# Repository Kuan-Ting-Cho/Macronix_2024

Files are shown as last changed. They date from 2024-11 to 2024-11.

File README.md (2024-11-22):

# Macronix_2024
[Human-Robot Collaboration of Intelligent Bipedal Robots in MultiLevel Warehousing_report](https://github.com/Kuan-Ting-Cho/Macronix_2024/blob/main/Human-Robot%20Collaboration%20of%20Intelligent%20Bipedal%20Robots%20in%20MultiLevel%20Warehousing.pdf)
## 競賽影片
競賽影片 (https://www.youtube.com/watch?v=QOL8G59Ion0)
## 模擬影片
模擬影片 (https://www.youtube.com/watch?v=DtHmWgVyCPI)
## 優勝獎
[第二十四屆旺宏金矽獎 半導體設計與應用大賽 優勝獎_獎狀](https://github.com/user-attachments/assets/30253aed-6e60-4f00-baa1-990223924b51)
## International and System Science and Engineering 2024 (ICSSE 2024)
[ICSSE 2024 conference paper](https://github.com/Kuan-Ting-Cho/Macronix_2024/blob/main/Mechanism%20and%20System%20Design%20of%20Linkage%20Driven%20Humanoid%20Robot.pdf)\
[ICSSE 2024_獎狀](https://github.com/user-attachments/assets/f3b2eac2-80f3-41f5-9eda-311fcf2eda83)

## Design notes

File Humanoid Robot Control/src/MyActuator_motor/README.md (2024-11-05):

# MyActuator_motor
This is the basic control of MyActuator motor using CAN bus communiccation. 
Basic setup and tutorials are in HackMD (https://hackmd.io/TwwChWEaTb-me8Ldjc6JkA?view).

NOTE: If you want to use Waveshare USB-CAN-A, then you neet to modify the file "serial_can.py" in original CAN package.
This is because Waveshare USB-CAN-A has unique frame format that is not supported in original CAN package. The CAN package I used in 2023/12/22 is python_can 4.3.1, there are some differences between each version. Be careful to use. And... good luck!

The latest pre-release can be installed with:
 '''
 pip install --upgrade --pre python-can
 '''

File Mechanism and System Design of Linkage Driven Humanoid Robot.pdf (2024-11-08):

Abstract— In this study, we present the design and implementation of a new humanoid robot lower body hardware structure. A four-bar linkage mechanism is used for the transmission to mimic the human leg muscles. The foot sole is designed to mimic the human arch, so that the robot can walk similar to the human gait. In addition, a comprehensive system architecture is established to control the robot.

I. INTRODUCTION

The humanoid robot has achieved a new milestone with the launch of the Tesla Optimus Gen 2 prototype [1]. In this paper, a new humanoid robot is proposed to mimic the human leg structure and the arch of the foot through a four-bar linkage mechanism [2] and foot soles design [3]. On the basis of high extendibility and maintenance, deep learning and algorithms are implemented to optimize and improve the robot system, ensuring that the robot can perform a variety of human actions and solving the phenomenon of labor shortage in modern industries.

II. METHODS AND RESULTS

The goals of robot’s leg design are to achieve light-weighting and mimic the structure of human legs which allows the center of mass of the bipedal robot to move upward, thus decreasing rotational inertia. In Fig. 1, Four-bar linkage mechanism is used for driving robot’s legs. This mechanism mimics the muscles contraction of human legs. All of four-bar linkages are parallel equal crank linkages. Except for the robot's driving links, which are made of high stiffness metal, lightweight materials are used. Carbon fiber tubes are used to connect the joints in the legs.

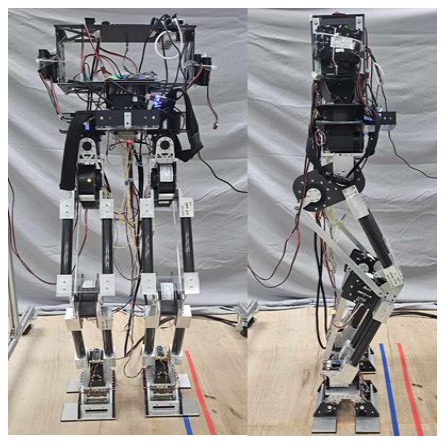
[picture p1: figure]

Figure. 1. The mechanism of the robot.

This work is supported by the National Science and Technology Council, Taiwan, R.O.C., under Grant NSTC 112-2221-E-006-155. The authors are with the aiRobots Laboratory, Department of Electrical Engineering, National Cheng Kung University, Tainan 70101, Taiwan ROC. (e-mail:
poetrydynasty@gmail.com, | j0988993487@gmail.com, | n26114201
@gs.ncku.edu.tw, n26114219@gs.ncku.edu.tw).
* Corresponding author: T.-H. S. Li (TEL: 06-2757575 ext.62363, E-mail: thsli@mail.ncku.edu.tw).

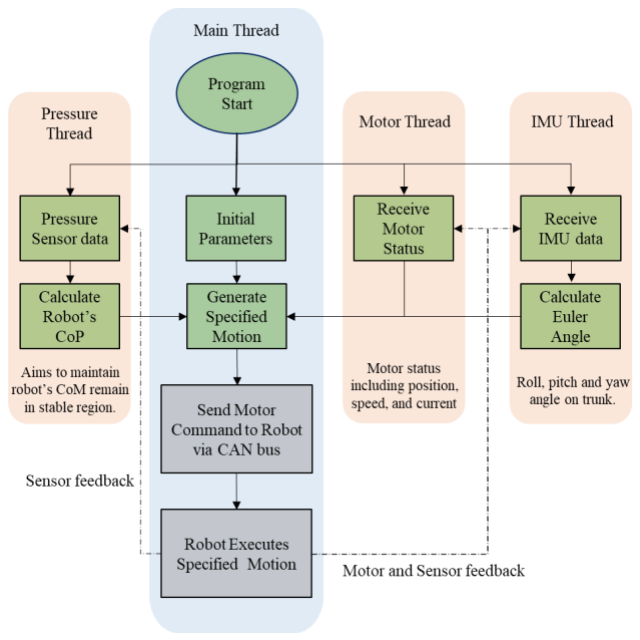
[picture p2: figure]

Figure. 2. The system architecture of the robot.
Regarding the design of foot soles, in order to reduce vibration during interaction with the environment, the mechanism mimics the arch of the human foot. Additionally, passive, rotatable joints are used at the front toe and rear heel sections as shown in Fig. 1.
The system architecture of this robot is shown in the Fig. 2. The control program consists of four threads, including the main thread and three others dedicated to receiving sensor data. The main thread is responsible for controlling the start and stop of each thread, receiving sensor data to generate appropriate motion commands, and transmitting them to the motors via the CAN bus. The other three threads are used to receive IMU data and compute Euler angles, receive motor angles and speeds, as well as receive pressure sensor data from the foot soles and calculate the robot’s center of pressure.

III. CONCLUSION
This paper presents an innovative design for a humanoid robot's lower body mechanism and system architecture, as well as the physical assembly and testing. In future work, we will finish the upper body of the robot and operate it to complete the walking and other dynamic testing so that it can be used in an actual-life situation.

REFERENCES

[1] “Optimus - Gen 2” https://www.youtube.com/watch?v=cpraXaw7dyc (accessed 2024/03/27.)
[2] Y. Zhang, L. Zhang, W. Wang, Y. Li and Q. Zhang, “Design and Implementation of a Two-Wheel and Hopping Robot With a Linkage Mechanism,” in IEEE Access, vol. 6, pp. 42422-42430, 2018.
[3] J. Sun, Z. Wang, M. Zhang, S. Zhang, Z. Qian, and J. Chu, “A Novel Metamorphic Foot Mechanism With Toe Joints Based on Spring-Loaded Linkages, ” in IEEE Robotics and Automation Letters, vol. 8, no. 1, pp. 97-104, Jan. 2023.

Kuan-Ting Cho, Chao-Chi Lee, Wei-Hsiang Huang, Yen-Ming Chen, and Tzuu-Hseng S. Li*

## Mechanism and System Design of Linkage Driven Humanoid Robot

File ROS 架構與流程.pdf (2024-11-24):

## ROS 架構與流程

節點與功能:

節點名稱 | 訂閱主 題 | 發布主題 | 功能描述
soldier | command | sensor | 接收馬達指令執行動作，計算感測器數 據，並發布感測器狀態
commander | sensor | command | 訂閱感測器數據，計算並生成執行動作與 平衡控制，並發布馬達指令

主題與數據:

主題名稱 | 資料來源 | 資料描述
sensor | soldier | 包含 IMU、壓力感測數據，以及馬達當前狀態
command | commander | 包含馬達目標位置、速度與控制模式指令

流程圖:

- [soldier 節點] →發布→ [sensor 主題] →訂閱→ [command 主題]
- [commander 節點] →發布→ [command 主題] →訂閱→ [sensor 主題]

節點詳細流程:

listener.py（接收指令並執行動作）

主要功能：

- 訂閱 “command” 主題，接收來自 “commander”的馬達指令。
- 根據收到的馬達目標指令與模式執行動作。
- 蒐集感測數據（IMU、壓力感測器），並發布到 “sensor” 主題。

核心流程：

- 初始化節點 “soldier”。
- 訂閱 “command”主題，更新當前馬達目標狀態。
- 執行動作（蒐集下一步的馬達狀態）。
- 周期性蒐集感測數據（IMU、壓力感測器）。
- 將馬達狀態與感測數據組合後發布到 “sensor” 主題。

talker.py（控制與指令發布）

主要功能：

- 訂閱 “sensor”主題，獲取感測器數據與馬達當前狀態。
- 執行動作控制，計算下一步馬達指令。
- 將計算結果發布到 “command”主題。

核心流程：

- 初始化節點 “commander”，建立訂閱與發布管道。

數據接收：

- 訂閱 “sensor” 主題，更新全域變數。
- imu_data：IMU 資料，用於平衡控制。
- l_fsr 和 r_fsr：左右腳壓力感測數據。
- pos：馬達當前角度。

動作生成與控制：

- 載入動作序列（CSV 文件中的馬達位置動作）。
- 插值生成平滑動作曲線，並根據感測數據控制目標馬達位置。
- 將馬達指令（目標角度、速度、模式等）發布到 “command” 主題。

“sensor” 主題（由 “soldier” 節點發布）

[[馬達 1 ID, 當前角度, 當前速度, 扭矩],

[馬達 13 ID, 當前角度, 當前速度, 扭矩],

[IMU_roll, IMU_pitch, IMU_yaw], [左壓力傳感數據 1, ..., 左壓力傳感數據 4], [右壓力傳感數據 1, ..., 右壓力傳感數據 4]]

“command”主題（由 “commander”節點發布）

[[馬達 1 ID, 控制模式, 目標角度, 目標速度, 扭矩, kp, kd],

[馬達 13 ID, 控制模式, 目標角度, 目標速度, 扭矩, kp, kd]]

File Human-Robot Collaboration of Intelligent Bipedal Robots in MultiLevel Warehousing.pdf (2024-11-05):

第二十四屆旺宏金矽獎

作品企劃書

# 智慧雙足機器人應用於多層 倉儲之人機協作

# Human-Robot Collaboration of Intelligent Bipedal Robots in Multi-Level Warehousing

## 參賽組別：應用組

## 參賽編號：A24-073

隊 | 長：卓冠廷
隊 | 員：李照棋、黃瑋翔、陳彥銘

摘要
本企劃設計及應用身長 126.4 公分之雙足機器人，著眼於下半身機構應用， 加入機構設計的巧思並開發系統架構，結合多種感測器資訊去對雙足機器人進行 控制。
在設計方面，團隊根據人體肌群，以四連桿傳動方式對機器人重心做調整， 不僅節省能源消耗，更是簡化機器人控制層面的難易度，同時也參考人體足弓， 設計了具緩震效果的腳掌，降低馬達與機構損耗，克服地形限制，更是讓雙足機 器人動作切合實體人類步態模式。
在應用方面，首先得建立雙足機器人步態數學模型，團隊成功將其運用於實 體機器人上，接著透過三種不同的場域測試進一步驗證，有負重走路、上下階梯 與不平坦地形的實驗，主打搬運機器人於多層倉儲會遇到的情境去研發，在基礎 的系統架構上加入不同演算法、強化學習等方式進行控制，最終成功將模擬的成 果於實體雙足機器人實踐。

一、前言
在現今社會中，高齡化對社會的影響越來越劇烈，缺工已成為產業難以解決 的問題之一，再加上 COVID-19 疫情的爆發，導致全世界的缺工問題更加嚴重。 在這樣的環境下，如果能將機器人應用於一些工作場域或是代替人類執行某些任 務，就能夠大大解決此問題。實際上目前許多工作場域都有慢慢引入機器人來替 代簡易的工作，但可以發現這些機器人的工作場域常常侷限於平面地面，無法跨 越樓層所帶來的限制，而雙足機器人則不受該種地形帶來的限制影響。 足型機器人在斜坡、階梯上往往較其它機器人有優勢。在空間沒有這麼寬廣 的超市倉儲內，雙足機器人因其下半身的獨特性，能更好地在該環境下移動。近 年來，越來越多公司投入雙足機器人的研發，如 Agility Robotic 的 Digit [1]、Boston Dynamics 的 Atlas [2]還有今年 Tesla 全新發表的 Optimus Gen 2 [3]，顯示出世界 知名公司也都致力於發展雙足機器人領域。然而，國內對於此方面的投入卻相對 十分稀少。最主要的原因在於此種機器人研究往往需要投入大量的資源才能夠實 現。因此，本計畫之一大目標便是利用這有限的資源，進行雙足機器人的開發和 研究，使其具備人機協作，甚至是不同機器人間的相互合作。

二、雙足機器人

1. 機構設計理念與目的
本團隊目前已開發雙足機器人的下半身機構如圖 1 與圖 2，同時也建立了 雙足運動數學模型。為了提高行走效率、儲存能量以及釋放動能，參考了人類腿 部結構與足弓進行設計。透過彈簧、馬達、連桿等各種元件的結合去建立了一個 強健的機構，同時具備緩衝功能，以極大程度地減少機體損傷的風險。此外，步 態模型的建立與感測器的回傳資訊實現了對機器人的精確掌控，使其能夠完成多 種預期中的行為和動作。
為了符合提出的應用場域，雙足機構的機構設計標準是輕量化以及減少能

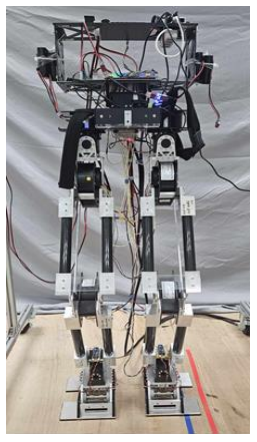
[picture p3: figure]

圖 1、機器人側視圖. | 圖 2、機器人正視圖. | 圖 3、機器人 CAD 圖.
量浪費，除此之外還需要有搬運重物的能力。透過模仿人類腿部的構造，讓雙足 機器人在運動過程中，可降低機器人與環境互動時所造成的振動，並運用連桿機 構傳動方式，使馬達能配置於臀部，提高雙足機器人腿部的重心位置，其目的是 增加腿部的靈活性，且由於執行需要抬腿的運動時，提高腿部重心能降低旋轉慣 性，同時也能降低馬達輸出時所消耗的能量，以增加馬達的壽命。 傳動方式上採用了四連桿機構如圖 3 反藍部分，透過連桿轉動使關節隨連 桿距離變化產生轉動，如同人類透過肌肉收縮使關節彎曲。使用四連桿的優點 有以下幾點，首先，可以將腿部的重心拉高，不需要將馬達配置在轉動關節位 置上，有效降低雙足的旋轉慣性，馬達也相對省力，再者使用四連桿可以限制 關節的轉動角度範圍，即使馬達突然失控也不會輕易造成機構受損，最後，雙 足機器人上的四連桿皆為平行四連桿，也就是說在關節限制範圍內，控制關節 的角度不需要考慮換算問題，馬達變動的角度即是關節屈伸的角度。 板材的部分主要以鋁件、POM、碳纖維板三者進行組裝，選材部分掌握一 些原則，如轉動摩擦的關節或需攻牙處需用鋁件，其餘則以碳纖維或 POM 材 質，連結關節轉動的部分使用光軸加上 C 型扣環，因其為受力點也是轉動點， 因此轉軸需要是金屬件降低摩擦並確保不容易形變，而 C 型扣環是防止關節之 間的相對滑動。板材雖然相對輕巧，但在強度上容易產生彎曲(bending)，由於 機器人總長 126.4 公分，腿長即佔 102.1 公分，若只用板材勢必要選剛度高的材 料，但這會相對增加機器人總重，因此採用管材並設計套筒去連接關節。為了 達到輕量化的目的，這裡選用了碳纖維管，碳纖維管不只具備了輕巧優勢，在 強度上也符合要求。
腳底板的設計如圖 4，為了降低與環境互動的震動和使雙足機器人行走能 夠更像人類的動作，外觀的設計上模仿了人類的足弓，並在前腳尖與後腳跟的 位置加上被動可旋轉的關節，原因是人在行走過程中前腳是腳跟先著地，而後 腳起步時腳尖是最後離地，透過這個被動旋轉的機構，使行走上能更貼近人類 步態。為達到被動旋轉的效果，採用了扭力彈簧如圖 5，扭力彈簧的彈力係數 不可以過小，否則容易造成機器人的不平衡，又因市面上扭力彈簧規格固定，

表 1、雙足機器人規格
高度(cm) | 126.4(腿長 102.1)
重量(kg) | 21.9
自由度 | 13
材質 | 碳纖維、鋁、POM

我們經過試驗方法去選擇合適的彈力係數，並在安裝時給彈簧一個預負載，使 其更有減振效果。旋轉軸的部分使用軸承加光軸的方式，並使用板件固定扭力 彈簧防止左右滑動如圖 5。

2. 系統架構:

A、硬體:
硬體除了設計理念中提到的部分，驅動主要由馬達來執行，馬達的部分採用 智能伺服馬達(圖 6)和盤式馬達(圖 7)作為驅動，前者具有高精度和高可靠性的特 性，同時支持多種通訊協定和控制模式，方便與其他元件協同工作，主要用於雙 足機器人的 Yaw、Roll 方向關節，即腰與臀部的關節，後者是一種無刷直流馬達， 具有高效率和低噪音的特性，並且內置了編碼器和驅動器，方便控制與調節，適 合用於雙足機器人的 Pitch 方向關節，即腿部的關節，帶動連桿進行傳動。 感測器的部分主要有慣性量測單元(Inertial Measurement Unit, IMU)(圖 8)以 及壓力感測器(圖 9)，前者用的是 Movella Xsens 開發的產品，其專精於慣性感測

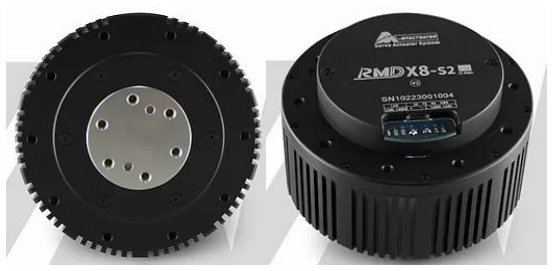
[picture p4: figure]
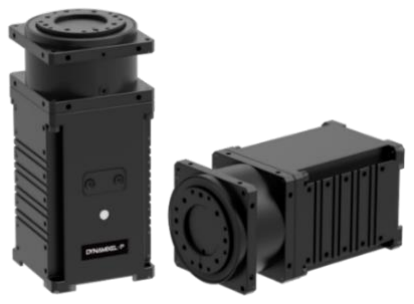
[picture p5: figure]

圖 6、智慧型伺服馬達. | 圖 7、盤式馬達.
圖 4、腳板側視圖. | 圖 5、扭力彈簧位置.

表 2、使用馬達規格表
| 智慧型伺服馬達 | 盤式馬達
重量(g) | 732 | 340 | 900
扭力(N.m) | 25.3 (at 24 V) | 5.1 (at 24 V) | 25 (at 48 V)
電壓(V) | 24 | 10.0~14.8 | 24、48
最大輸出 功率(W) | 132 | 20 | 110

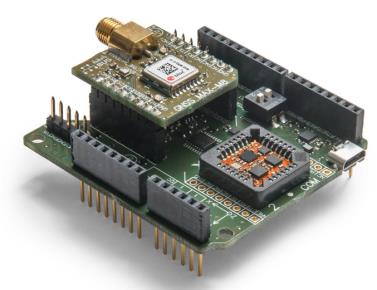
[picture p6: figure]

模組的設計生產與多傳感器融合演算法(Sensor Fusion)，我們將其配置於腰部， 蒐集機器人運動時的的尤拉角(Euler angle)、直線加速度與角加速度等資料，後者 選用薄膜壓力傳感器，置於腳底板四個角落，蒐集機器人運動時腳底受力狀況。

B、軟體:

系統的架構主要由四個線程(Thread)組成，分別有 Main Thread、Pressure Thread、Motor Thread、IMU Thread。主線程負責控制每個線程的啟動與停止， 接收感測器資料以產生運動命令，並透過 CAN bus 將其傳輸到馬達。另外三個 線程用於接收馬達角度、速度、IMU 與壓力感測器的資料。

(1)、感測器資料前處理與分析:

由於雙足機器人運用不同馬達進行運作，在接收馬達回傳值時，容易遇見回 傳時間不一的問題，因此在資料前處理上會適時的延遲，使馬達回傳時間盡量達 成一致，方便後續閉迴路控制做使用。IMU 的回傳資料則是經解碼後透過將四元 素轉換為尤拉角去使用，偵測機器人轉向之偏移幅度，作為步態修正之依據。壓 力感測器的量測需要根據機器人總重量去選擇合適的電阻值，資料前處理上會先

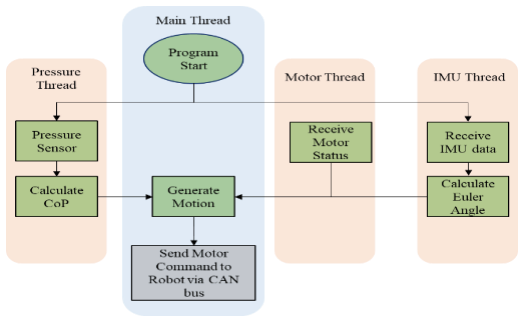
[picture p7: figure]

圖 10、雙足機器人之基礎系統架構

圖 8、Xsens MTI-7-DK IMU [4]. | 圖 9、薄膜壓力傳感器 [5].

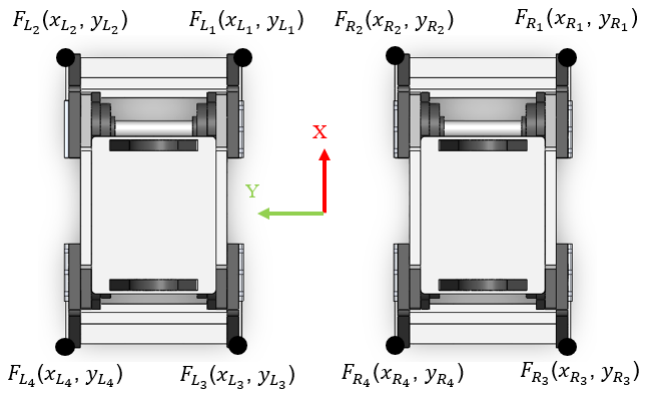
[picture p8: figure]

進行根據機器人實體情形進行雜訊濾波，防止因雜訊導致壓力中心位置的計算偏 差擴大，處理過後的資訊會用來分析機器人模型的 Center of Pressure(CoP)偏移。 壓力感測器裝置於機器人足部，左右腳的四個角落外圍各裝設一顆壓力感測器， 用夾層方式於腳底板與踏墊間加裝壓力感測器，如此一來，在機器人腳部未接觸 地面時，仍可繼續得到壓力偏移值，分別對雙腳各四個壓力感測器計算 CoP 之 x 與 y 位置，如(1)-(2)與圖 11 所示。

4 | 4
1 | 1
4 | 4
1 | 1
Ri | Ri | Li | Li
i | i
CoP
| Ri | Li
i | i
F x | F x
X
F | F
= | =
= | =
- | + | ·
=
| +
∑ | ∑
∑ | ∑
， | (1)
4 | 4
1 | 1
4 | 4
1 | 1
Ri | Ri | Li | Li
i | i
CoP
| Ri | Li
i | i
F y | F y
Y
F | F
= | =
= | =
- | + | ·
=
| +
∑ | ∑
∑ | ∑
。 | (2)

(2)、步態產生器數學模型:

為了讓雙足機器人能順利行走，一普遍且容易實現的步態模型為線性倒單擺 (Linear Inverted Pendulum Model, LIPM)，只需使用有限的物理結構資訊，即可生 成雙足機器人的步態。假設一個由點質量和無質量伸縮腿組成的倒單擺來模擬一 條腿支撐身體時狀況，其質心位置 x(t)以及質心速度ẋ(t)可以表示為:

x(t) = (x(0) − px) cosℎ cosℎ (
t
Tc

) + Tcẋ(0)sinℎ (
t
Tc

) + px，

(
3)

ẋ(t) =

(x(0)−px)
Tc

sinℎ sinℎ (
t
Tc

) + ẋ(0)cosℎ (
t
Tc

)。

(
4)
將此結論進一步推廣到三維的線性導單擺模型之中，分為 x-z 平面與 y-z 平 面進行推倒，得出 x 與 y 方向上的質心位置與速度，以實現的步行控制。之後將 LIPM 得出的結果透過特定的轉換即可套用於我們的機器人身上，生成出我們所 需要的動作。
為了能夠控制機器人的各關節，有必要進行一系列的數學推導來找出其中的 角度與位置關係。在機器人領域中，順向運動學（Forward Kinematics）是一個重

圖 11、壓力感測器安裝位置.

圖 12、機器人正視圖. 圖 13、機器人 45°視圖. 圖 14、機器人側視圖. 要的概念。它用來描述機械系統中各個部分相對於參考點或參考座標系的位置和 方向，透過順向運動學，可從給定的機械系統關節角度中，計算末端點的位置和 方向。為了建立出順向運動學，必須先定義出雙足機器人的 Denavit-Hartenberg （DH）表，DH 表的每一行需從機器人的前後關節找出資訊，其中包含四個參數：
1. θi： 繞著前一個 z 軸的角度，從舊的 x 軸到新的 x 軸。
2. di： 沿著前一個 z 軸到共同法線的偏移量。
3. ai： 共同法線的長度
4. αi： 繞著共同法線的角度，從舊的 z 軸到新的 z 軸。
透過 DH 表，我們可以在機器人的雙足上建立坐標系(圖 12-圖 14)。在設計 的機器人身上，每隻腳各有 6 個自由度，分別是髖關節上的 Yaw(R1, L1 )、 Roll(R2, L2 )與 Pitch 軸(R3, L3 )、膝蓋的彎曲 Pitch 方向(R4, L4 )以及腳踝的 Pitch(R5, L5)跟 Roll 方向(R6, L6)，其中 Z 軸為馬達旋轉方向，其中原點的部分設 置在髖關節中 Yaw 方向(R1, L1)旋轉的馬達中心，表 3 呈現雙足機器人的 DH 參 數。
表 3、雙足機器人的 DH 表.
i | θi | ai | αi | i d
1 | | | | d1

2

3 | 90° 0 | L2 L1 | −° 90 90° −° 90 90° L6 0 | 2 d L3 L4 L5 d3
4 | 2.74° | | 0 | 0
5 | -2.74° | | | 0
6 | 0 | | 0 | 0

1

cos | cos | sin | sin | sin | cos
sin | cos | cos | sin | cos | sin
0 | sin | cos
0 | 0 | 0 | 1
i | i | i | i | i | i | i
i | i | i | i | i | i | i | i
i
i | i | i

a
a
H
d
θ | α | θ | α | θ | θ
θ | α | θ | α | θ | θ
| α | | α

−

é | ù −
ê | | ú
−
= ê | | ú
ê | | ú
ê | ú ë | û
， | (5)

6
E

0 0 -1 0
0 1 0 0
1 0 0 0
0 0 0 1

H

é | | ù
ê | | ú
= ê | | ú
ê | | ú
ê | ú ë | û
， | (6)

式(5)顯示的是轉換矩陣，其包含了每個關節的位置與方向資訊，透過將 DH 表中的參數帶入，可以得出機器人每個關節的轉換矩陣。式(6)表示踝關節 Roll 方向的馬達座標到腳底板座標的轉換矩陣，式(7)表示了原點的坐標轉換到 末端點坐標:

| | | | | | | | | 11 | 12 | 13 | 0 ,
0 | 0 | 1 | 2 | 3 | 4 | 5 | 6 | 0 | 21 | 22 | 23 | 0 ,
E | 1 | 2 | 3 | 4 | 5 | 6 | E | E
| | | | | | | | | 31 | 32 | 33 | 0 ,

= P =

0 | 0 | 0 | 1 Ex
| | | Ey
| | | Ez
r | r | r | P
r | r | r | P
H | H H H H H H H
r | r | r | P
é | ù
ê | ú
= | ê | ú
ê | ú
ê | ú ë | û
。 | (7)

然而，在實際情況中，更多的時候我們已知機器人到達的目標位置，因此需 要反過來求得關節角度，這時就需要運用到逆向運動學(Inverse Kinematics)，而 每個關節角度可以透過式(7)左右等式相等來計算出，將線性導單擺模型規劃的 步態軌跡反推回每個馬達所需執行的角度命令，實現各式各樣的動作。

三、不同任務之實現

1. 負重靜態與動態平衡即時控制
A. 簡介
本章節會介紹雙足機器人在運送貨品時所需的靜態與動態平衡技術。由於本 團隊雙足機器人的行走步態是使用線性倒立擺模型控制機器人的行走軌跡，其為 開迴路的控制方法，若直接將貨品放到雙足機器人上行走，機器人會因重心不穩 而摔倒。因此本章節將針對此問題提出負重演算法以及平衡控制器，使雙足機器 人再負重時得以穩定行走，使其順利完成運送貨品任務。
B. 控制系統架構
圖 15 為本章節的控制系統架構圖，首先雙足機器人是由姿態控制器來做出 動態或是靜態的姿態，這裡所指的動態為 LIPM 產生的步態，靜態則是雙足機器 人的初始穩定姿態。根據姿態控制器的輸出，平衡控制器會決定要採用單腳或者 是雙腳的補償平衡，補償的多寡會由馬達當前狀態、慣性測量單元(IMU)和機器 人腳底板裝設的壓力感測器來決定。若是在靜態的情形下，雙足機器人會根據壓

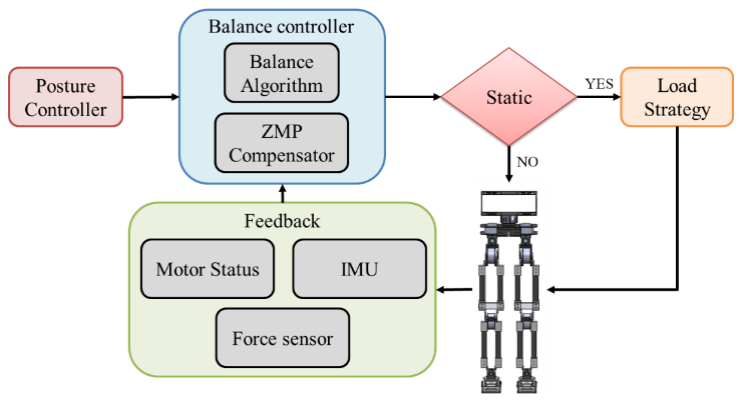
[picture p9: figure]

力感測器來判斷雙足機器人是否被裝載貨品，根據情況啟用負載緩衝策略，使機 器人不會因為裝載重物而失去平衡摔倒。最後總和所有控制器的輸出至雙足機器 人每顆馬達做出理想的平衡姿態。

C. 平衡控制器
無論雙足機器人的狀態為動態或靜態，所有良好的動作都是基於雙足機器人 在保持平衡的狀態下產生，因此保持平衡是不可或缺的要素。尤其對大型機器來 說，因為重心較高，在動作的控制上也會變得更加困難，因此為了使雙足機器人 有更好的表現，平衡控制器的存在成為關鍵。此章節所提出的平衡控制器分為兩 個部分，第一部分為平衡演算法，第二部分為零力矩點(ZMP)補償器，而兩部分 輸出的總和為平衡控制器的輸出。平衡演算法流程圖如圖 16，並分成靜態以及 動態。
首先雙足機器人在靜態時通常保持著雙腳對齊貼平地面，且質心投影位置在 雙腳中心的位置，以利接下來運動，然而外在環境的變化如地板傾斜或外力干擾， 會使質心偏離雙腳中心不利於下一個動作，甚至最嚴重導致摔倒，為了解決這個 問題，此演算法提供了適應環境變化的能力。根據兩隻腳的馬達角度回授，透過 順向運動學求得兩隻腳的末端執行器(End effector)位置以及旋轉矩陣，在前述所 提的靜止狀態下，左右腳的旋轉矩陣必定相同，由此可以得知雙腳末端執行器座 標相對質心座標的旋轉情況，而 IMU 回授可得知質心座標傾斜多寡，為了使質 心座標保持在平衡位置，此演算法將質心座標的傾斜角度乘上權重值後加入旋轉 矩陣，末端執行器位置也會隨著傾斜而調整，再透過逆向運動學映射回各個馬達 做即時補償，達到質心座標平衡的目標。
在動態的部分，步態週期分為單腳支撐和雙腳支撐兩種階段，支撐腳是行走 保持平衡的關鍵，此演算法主要是補償單腳支撐階段，因為雙足機器人在行走時 雙腳支撐是為了將重心轉移至另一支撐腳，其時間遠小於單腳支撐階段，因此演 算法將轉移重心前半段的支撐腳視為後腳，而後半段的支撐腳視為前腳。由於 LIPM 產生的步態質心座標並不會轉動，因此可以根據 IMU 回授做補償。動態補 償方式與靜態有兩點不同，第一是權重值較小，因為在行走情形下做較大幅度的

圖 15、負重平衡控制系統架構

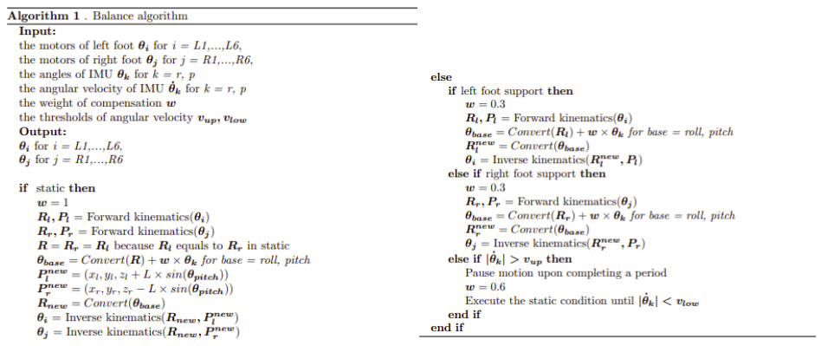
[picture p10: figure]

圖 16、平衡演算法
補償會導致質心速度方向改變太大，導致機器人摔倒，因此找到適合的權重值更 有助於行走時的穩定性，根據實驗結果在行走時權重值為 0.3 最穩定。然而在一 連串的動作下，雙足機器人可能會因外力導致質心速度改變偏離理想運動軌跡， 因此若發生質心速度高於平常穩定行走的閥值時，演算法會在完成當前行走週期 後將動作暫停，並進入暫時的靜態平衡直到質心穩定，此時的權重值不可與完全 靜態時相同，因為此時的質心較不穩定，若權重值太大會導致過度補償，根據實 驗結果權重值為 0.6 時可最快穩住質心。
在執行平衡演算法時，必須確保腳底板是貼平地面，因此提出零力矩點補償 器來解決此問題。根據腳底板的壓力感測器所回授的類比訊號，可以通過(8)至 (11)式獲得兩隻腳的零力矩點位置：

Zv =

(F1 + F4

)
(F2+F3+ε)
， | (8)

Zx =

Lx × Zv
(1 + Zv

)

−

Lx
2
， | (9)

Zℎ =

(F1 + F2

)
(F3+F4+ε)
， | (10)

Zy =

Ly × Zℎ
(1 + Zℎ

)

−

Ly
2
， | (11)

其中Zx、Zy為零力矩點座標，Lx、Ly為腳板的長與寬，ε為極小數值，其目的 是為了防止(8)、(10)式的分母為零，因為將座標零點設定在腳板中心如圖 17， 因此需要減去一半的腳板長寬。零力矩點補償器透過調整腳踝的 Roll 和 Pitch

圖 17、零力矩點座標參數示意圖

方向的馬達來達成目標，控制方式是採用 PD 控制器如下(12)、(13)式：

θi = Ki(Zi,y − Zi,y

d

) + Di(Ż

i,y − Ż
i,y

d
)， | (12)

θj = Kj(Zi,x − Zi,x

d

) + Dj(Ż

i,x − Ż
i,x

d
)， | (13)
其中i = R6, L6、j = R5, L5表式左右腳，因此補償器總共會有 4 組 PD 參數， 針對腳踝四顆馬達進行角度調節。然而要同時找到 4 組最佳的參數並不容易， 為了解決此最佳化問題，此章節使用元啟發式演算法根據設定好的訓練環境計 算適性函數(Fitness function)找尋最佳解，而訓練環境和適性函數的設計將影響 是否能找到最佳解的關鍵。
為了有效尋找，訓練環境由多階段的任務組成，其中包含地面旋轉、外力 干擾以及負重行走，任務總長為 2500 個時間步長(Time step)，每個時間步長為 0.02 秒，三個任務長度分別 1000、500、1000 時間步長，為了縮短總訓練時 間，當質心高度小於設定閥值時則判定雙足機器人摔倒提早結束訓練。在地面 轉動的任務會分為三個階段，其分別為對 Roll 方向旋轉、對 Pitch 方向旋轉、 對 Roll 和 Pitch 方向同時旋轉，旋轉方式如(14)式：

θ(t)ground =

π

18 × sin (
t × 2π
Tg
)， | (14)

其中Tg為地面轉動週期，長度為 250 個時間步長，在這時段內地面會依據設定 方向旋轉正負 10 度。在外力干擾的任務中，設定在指定時間點對機器人施予 195 N 的外力，其方向分為 x 和 y 方向。負重行走任務是在指定時間點會負載 重物，平衡後行走至時間結束，負載重量為 2 kg。
在適性函數的設計上，去計算左右腳每個時間步長在 x 與 y 的零力矩點座 標位置與速度與理想狀態差的絕對值，最後將所有值總和作為其訓練適性值 (Fitness value)，然而因為有提早結束訓練的機制存在，在被判定提早結束時， 必須將剩餘的時間不長皆給予懲罰分數，否則在訓練時演算法會為了得到最小 的適性值而選擇讓機器人摔倒。適性函數如下：

Lx,i = abs(Zl,x − Zl,x

d

) + abs(Ż

l,x − Ż
l,x

d
)， | (15)
Ly,i = abs(Zl,y − Zl,y

d

) + abs(Ż

l,y − Ż
l,y

d
)， | (16)

Rx,i = abs(Zr,x − Zr,x
d

) + abs(Ż

r,x − Ż
r,x

d

)， | (17)

Ry,i = abs(Zr,y − Zr,y
d

) + abs(Ż

r,y − Ż
r,y

d

)， | (18)

F = p × (T − k) + ∑ Lx,i + Ly,i

k
i=0
+ Rx,i + Ry,i， | (19)

其中Lx,i、Ly,i、Rx,i、Ry,i為左右腳 x 與 y 方向適性值，在(19)式中F為最後適性 值，p為懲罰分數，T為總時間步長，k為完成之時間步長。 在訓練用的元啟發式演算法採用較為經典的粒子群演算法(PSO) [6]執行訓 練，其演算法流程圖如圖 18，此算法是源於對生物群體行為的模擬，如鳥群或 魚群的集體行為。它通過粒子在搜索空間中的移動，以找到最佳解。PSO 的原

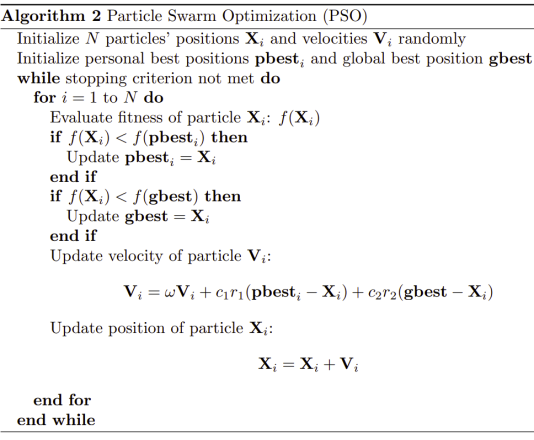
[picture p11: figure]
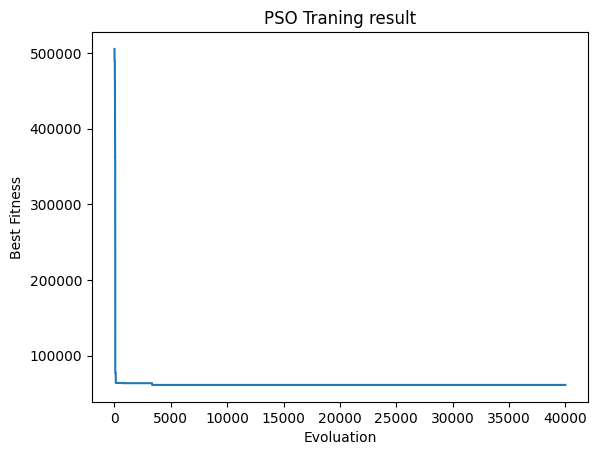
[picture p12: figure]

圖 18、PSO 演算法流程 | 圖 19、PSO 10 次訓練平均適性值變化
理相對簡單，但卻能在許多問題中展現出強大的搜索能力。因為每次訓練的收 斂結果會有所不同，也有可能陷入局部最佳解，為拿到最佳的參數，將透過數 次的訓練並採用最佳適性值的參數作為零力矩點補償器的控制參數。訓練 10 次 平均收斂結果如圖 19，在計算適性值的位置和速度單位使用毫米和毫米每秒， 可根據訓練結果最佳適性值為 57138，在除以總時間步長後，平均每個時間步 長所得之適性值為 22.85，由此可知偏移量很小，可以確保腳底板在執行平衡演 算法時平貼於地面。
D. 負重策略

負重策略是模仿人在搬取重物時，會先藉由膝關節緩衝並藉由髖關節調整身 體重心，以此快速達到穩定，為了幫助雙足機器人從未負重至負重的階段起到 緩衝效果，並加速讓機器人取得平衡，策略流程圖如圖 20，此策略為快慢補償 同時進行的策略，Knee strategy 為快速補償，Hip strategy 為慢速補償。 首先介紹 Knee strategy，此策略是根據壓力感測器是否有感受到外來重量 而啟動，在偵測到外來重量時，Knee strategy 會透過快速改變膝關節角度幫助 機器人做緩衝，降低外物衝擊對機器人造成的不穩定性，補償方法如(20)、(21) 式：

θknee = β × a × sin (
s×π

2Tknee

) + B， | (20)

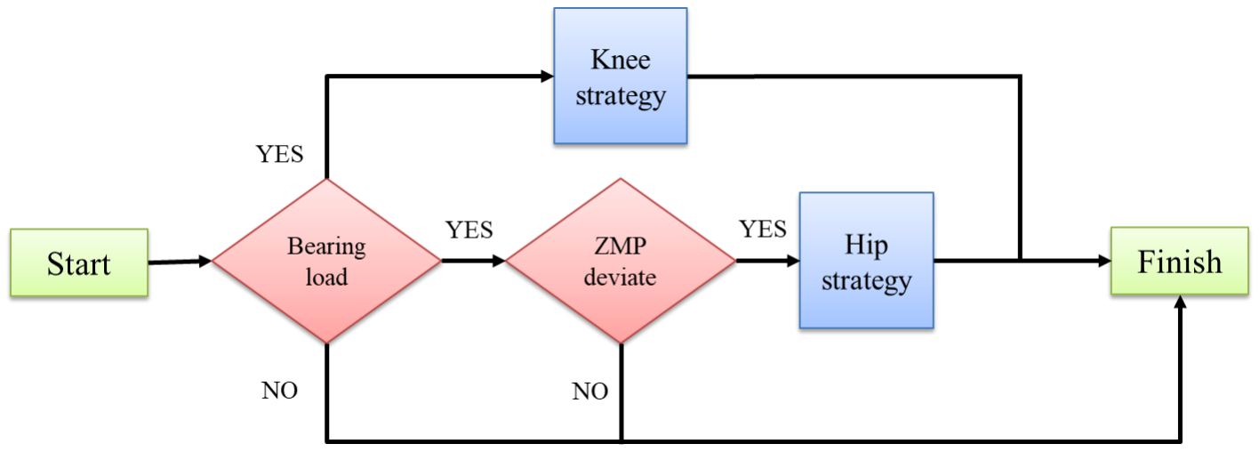
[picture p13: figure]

圖 20、負重策略流程圖

st+1, at+1, Bt+1 =
{
st+1 = 5, at+1 = θt+1

pitcℎ
, Bt+1 = Bt

,
st+1 = st + 1, at+1 = at

, Bt+1 = Bt

,

st+1 = 1, at+1 = θt+1

pitcℎ
, Bt+1 = Bt + at × β,

if |θt+1

pitcℎ
| > |at
else if st < Tknee
else st = Tknee

，

(21)

其中θknee為補償θR4、θL4的角度，β為補償權重，a為當前傾角絕對值的最大 值，s為迭代計數參數，Tknee為補償週期，B為累計過去補償值。這個策略分為 三個階段，第一階段為穩定質心，此階段 IMU 回授質心座標傾角持續擴大，此 時s維持定值而a持續更新，直到傾角減小，此時θknee會隨著a更新而快速增 加，幫助快速穩定；第二階段為快速回正，此時通過迭代增加s而a維持定值， 通過 sin 波的補償快速回到傾斜程度較低的狀態；第三階段為微幅調整，在s完 成一次周期後重新計算，a會根據更新當前傾角值，B累計目前已補償角度，藉 此回到最初未傾斜狀態。
Hip strategy 主要是透過調整髖關節的 pitch 方向馬達使雙足機器人重心保 持在雙腳中心，補償方式如(22)式：

θaccu

k+1 = θaccu

k + γ ×

Zr,x + Zl,x
2
， | (22)

其中θaccu為 Hip 累計補償角度，γ為補償權重，此方法式根據零力矩點的位置 做迭代累計補償，透過這個方式可讓重心穩定靠近雙足的中心點，雖然只能無 限接近中心點無法到達，但只要讓重心足夠靠近中心點，雙足機器人就可以保 持良好的平衡姿態。
兩種策略是以同時補償的方式使機器人快速回到穩定狀態，為了不讓兩種 策略相互衝突，補償方法如(23)至(26)式：
θR3

k+1 = θR3

k + θaccu
k+1 ， | (23)
θL3

k+1 = θL3

k + θaccu
k+1 ， | (24)
θR4

k+1 = θR4

k + θknee − θaccu
k+1 ， | (25)
θL4

k+1 = θL4

k + θknee − θaccu
k+1 ， | (26)
在(25)、(26)式通過扣掉 Hip strategy 的補償角度，使雙足機器人在姿態上能保 持平衡。
為了驗證本章節所提出的控制系統，本團隊在先在模擬環境運行測試，其 流程如圖 21。在環境中，雙足機器人被賦予載運 2kg 的紅球前行的任務，可以 看到機器人在保持平衡狀態後，順利運用平衡控制器與負重策略，在負重平衡 後穩定的行走。

圖 21、負重平衡到行走流程

2. 上下樓梯任務設計與實現
A. 簡介
由於調整 LIPM 參數是一件非常繁瑣複雜且耗時的事情，且同樣的參數並 不適用於各種情況，因此本計畫設計一款基於 Twin Delayed DDPG (TD3) [7, 8] 深度強化學習的回授控制系統，如圖 22，能夠讓機器人針對當前的外界情況預 測出最適當的 LIPM 參數，並藉此達到穩定行走。
B. 基於人體前庭脊隨反射機制的可變質心高度 LIPM 步態模型 為了讓雙足機器人能夠更好得適應地形，這部份我們參考了人類在行走時的 前庭反射機制 [9]，這項機制使人類能夠維持平衡並克服外在的各種干擾，因此 我們將此套用在雙足機器人上，可以使機器人擁有自適應的穩定能力，從而避免 摔倒的情況發生。在上下樓梯的任務當中，機器人的質心軌跡變化大致如圖 23 所示，在上樓梯行走時，系統反饋迴路被設計成驅動身體質心沿著樓梯向前移動， 同時減少步幅長度以維持動態穩定性；相反地，在下樓梯行走時，身體質心將向 後移動，步幅長度將增加以防止失去平衡，如此一來就能確保機器人在行走過程 當中的穩定性。
在本作品當中，上下樓梯的步態模型是基於線性倒單擺模型 [10, 11]生成 的，但傳統的 LIPM 模型假設機器人的質心高度是恆定不變的，使得此步態模 型只適合用於雙足機器人於平地行走的情形，考量到這點，我們決定加以改變 行走時的質心軌跡，使其更適應於垂直移動的任務。原始的 LIPM 軌跡相

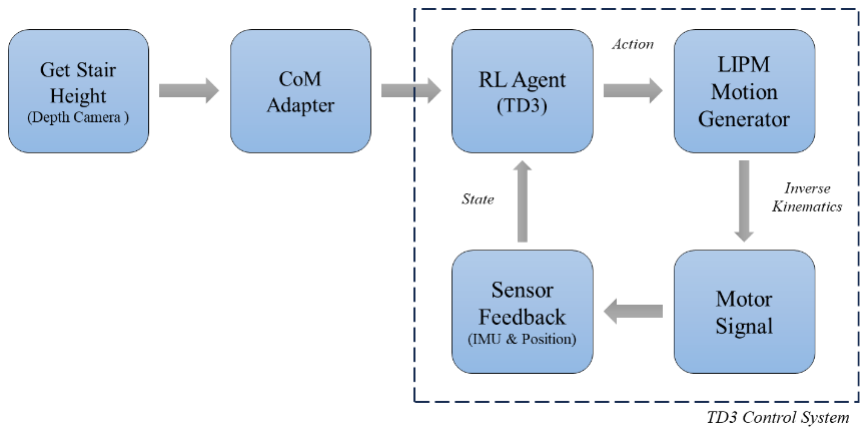
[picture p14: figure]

圖 22、TD3 回授控制系統

(a) | (b) | (c)
| 圖 23、機器人面對樓梯地形時的重心姿態。
| (a)上樓梯 (b)行走於平面 (c)下樓梯

對於世界座標在垂直方向上的變化如式(27):

wfootz

(t) = {

H
2
(1 − cosθ), | for t1 < t < t2
0, | otℎerwise
， | (27)
Rfootz =w footz−wCoMz， | (28)
其中 H 是機器人的抬腳高度，t1 及 t2 分別是雙腳支撐及單腳支撐的時間，θ則 為2π(t − t1

)/(t2 − t1),t ∈ (0, T)，相對於機器人座標的表示即為式(28)。接下來 為了適應行走時不同的高度，我們加入了一個變化項，這裡定義為式(29)，此 變化項能夠使機器人抬腳的高度隨著行進中去做最佳的調整，最終可變質心高 度的 LIPM 在垂直方向上的軌跡變化為式(31)所示，其雙腳軌跡圖則如圖 24。 aCoMz = −ACoMz
⋅ S(t)， | (29)

S(t) = {

0, if t < t1
t − sin (t)
2π
, | otℎerwise
1, | if t > t2
， | (30)
footz =w footz−wCoMz−aCoMz。 | (31)
C. TD3 演算法

在強化學習當中有多種演算法可以使用，像是 DQN [12]、PPO [13]及 DDPG [14]等，這些演算法雖然都有各自的特點，但也有些不足的地方，像是 DQN 通常需要大量的樣本進行訓練導致學習過程較慢；PPO 容易陷入局部最佳 解的情形；還有 DDPG 對超參數較為敏感不易調整，此外 DDPG 還有一個常常 失敗的原因，就是訓練過程中所學習到的 Q 函數容易高估 Q 值，這導致了策略 被破壞。TD3 則是為了解決此問題所開發的延伸演算法，其引入了三個方法來 解決此一問題，第一點是 TD3 會學習兩個 Q 函數，並使用其中較小的 Q 值作 為貝爾曼誤差函數當中的目標；第二是延遲策略的更新，TD3 對於策略的更新 頻率低於 Q 函數的更新頻率，在 [7]當中建議更新 0 率為 1 比 2；第三則是平 滑化目標策略，TD3 會在目標動作當中添加雜訊，並透過平滑 Q 值，使策略更 難利用 Q 函數中的錯誤，透過這三個方法 TD3 彌補了 DDPG 中的不足。

(a) | (b) | (c)
圖 24、傳統 LIPM 與自適應 CoM LIPM 的雙腳高度在垂直方向上的變化。 (a)傳統 LIPM (b)改良式 LIPM 上樓梯 (c)改良式 LIPM 下樓梯

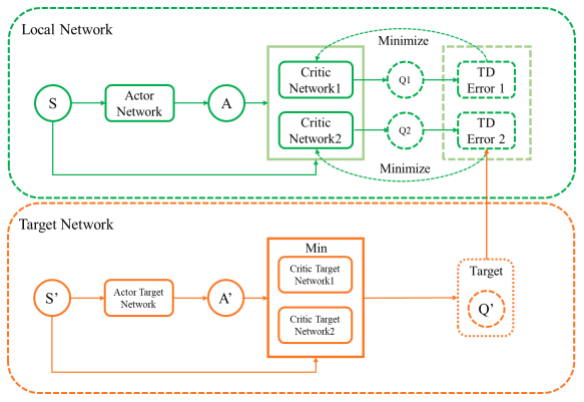
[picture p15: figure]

圖 25、TD3 架構圖
接下來看一些 TD3 當中重要的方程式，首先是目標策略平滑的部分，組成 Q-learning target 當中的動作都是基於目標策略μθtarg，TD3 在動作的每個維度 上都會添加 clipped noise，使得目標動作會被限定在有效的動作範圍之內，因此 目標動作被寫作:

a

′(s

′) = clip (μθtarg(s

′) + clip(ε, −c, c), aLow, aHigℎ) , ε ∼ N(0, σ )， (32)

平滑目標策略的本質上是作為此演算法中的正則化器，它解決了 DDPG 當中的 錯誤估計尖峰。

其次是 clipped double-Q learning，這兩個 Q 函數都使用單個目標，該目標是 使用兩個 Q 函數當中較小的一個來作計算:

y(r, s

′
, d) = r + γ(1 − d) min
i=1,2

Qφi

,targ (s
′
, a

′(s

′))， | (33)

然後兩者透過回歸到此目標來學習:

L(φ1, D) = E
(s,a,r,s

′
,d)~D

[(Qφ1

(s, a) − y(r, s

′
, d))

2
] ， | (34)
L(φ2, D) = | E
(s,a,r,s

′
,d)~D

[(Qφ2
(s, a) − y(r, s

′

, d))

2
]。 | (35)

使用較小的 Q 值做為目標值，然後逐步回到該值，有助於避免 Q 函數被高估。 最後策略會以最大化Qφ1為目標來學習:

max
θ

E
s~D

[Qφ1

(s, μθ

(s))]。 | (36)

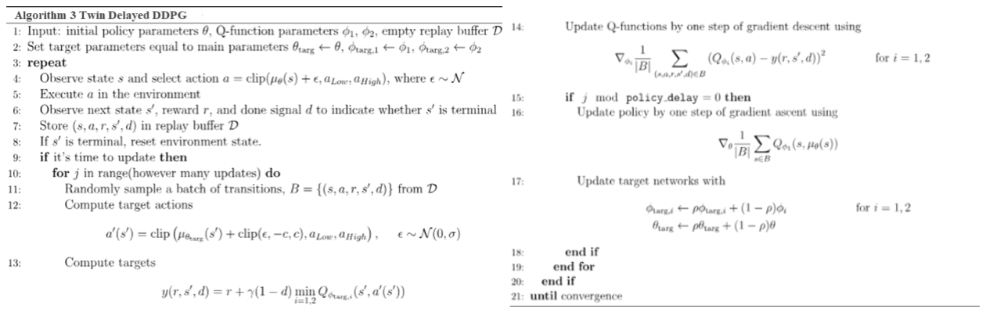
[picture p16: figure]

圖 26、TD3 Pseudocode [8]

圖 27、系統流程圖

D. TD3 控制系統
為了要增強機器人在爬樓梯過程當中的穩定性及強健性，本作品將前段所提 到的 TD3 強化學習構建成一個回授系統並用於此任務，整個系統流程如圖 27。 在策略開始運作後，機器人首先會先獲取前方地形的高度，或是由操作者手動輸 入，機器人會根據此數值來調整自身的 CoM 高度，藉以達到最穩定的姿態，接 著再開始行走，行走的動作指令如前述是由 LIPM 模型生成的，再透過逆向運動 學映射到每顆馬達上，並且在行走的過程當中蒐集外在的環境資訊，這些資訊會 作為當前 RL agent 的狀態，接著 RL agent 會預測出下個時間點的動作並丟進 LIPM 當中，如此反覆以此達到即時的回授控制。
E. RL 強化學習架構

RL 作為此任務當中的重要角色，這一章節將說明 RL 的狀態以及獎勵函數 等定義。
圖 28 為 RL 的流程圖，其中模型的輸入及輸出如下說明，環境狀態，也就 是模型的輸入如式(37)，

st = [Qbase, abase, pmotor, Hstair]，
Qbase = [w,i,j, k]

T，

abase = [ax, ay, az

]

T。

(37)

其中的Qbase是在機器人 base 所量測到的四元數，abase是 base 在 xyz 方向上的加 速度，pmotor是每顆馬達當下的角度位置，Hstair則是前方樓梯的高度，訓練過程 中有將Hstair做強化，以便在 RL 訓練當中更有效地辨認出此資訊，因為樓梯高 度會對行走的過程產生非常大的影響。

圖 28、RL 流程圖

另外模型的輸出則如式(38):

at = [BR,BL
, SR, ℎR, ℎL

, HR, HL

,AR,AL

]。 | (38)
先前有提到 RL 的輸出動作會作為 LIPM 的輸入參數，因此這些數值都與機器 人的行走相關，其中的 B 代表步行過程中機器人左右擺動的幅度、S 是跨步的 長度、h 是抬腳過程中髖關節擺動幅度、H 是抬腳的高度、A 則是腳踝在 pitch 方向上傾斜的角度。
RL 的獎勵函數更是重要的一環，定義好的獎勵函數能夠讓訓練過程更加有 效率，在此任務中須考量到的層面有很多，主要都跟機器人的狀態有關，首要 目標還是希望機器人在執行任務過程當中能夠穩定且高效，因此本作品定義的 獎勵函數如下:
R = w1RCoP + w2Rmove + w3Rstable + w4Rℎealtℎy， | | (39)
RCoP = (1 − P) ⋅ (−√xlCoP
2 + ylCoP

2

) + P ⋅ (−√xrCoP
2 | + yrCoP
2 | )， | (40)

w2 = [w21, w22, w23]，
Rmove = w21xdistance − w22|ydeviation| − w23|θyaw|， | | (41)

Rstable = |αx

| + |αy| + |αz
|， | (42)

Rℎealtℎy = {
1, | for every timestep
−10, | if robot fall down
20, | if mission success
。 | (43)

本實驗設計的獎勵函數分成四個部分，第一是RCoP，這項獎勵是用來評估機器 人的重心位置是否落在腳底板的穩定區域內，因為若當機器人的重心位置離開 了穩定多邊形區域，機器人極有可能會摔倒；第二是Rmove，主要用來鼓勵機器 人能夠向前行走，並且要避免發生 y 方向或 yaw 方向的不自然偏轉，其中的w2 是分別的權重，會在下一章進行說明；第三是Rstable，這是一個懲罰項，用來 衡量機器人 base 的加速度，對於穩定行走來說，我們當然希望加速度會越小越 好，因此給定此一懲罰；第四是Rℎealtℎy，此獎勵項有兩個功用，其一是彌補其 他懲罰項所帶來的負值，其二是在任務完成或失敗的狀態下給予獎勵或懲罰， 在本任務當中失敗的定義就是機器人摔倒或是偏轉太多，成功走上階梯則定義 為成功的狀態。

F. 實驗與模擬
(1)、訓練過程
上一章所提到的獎勵函數當中的參數如表 4，負號代表的即是懲罰項，這 些參數的選擇是考量到各獎勵項之間數值大小的差異而給予不同的倍數，也有 表 4.獎勵函數中的參數
w1 | 2 | w23 | -5
w21 | 0.5 | w3 | -1/3
w22 | -2 | w4 | 1

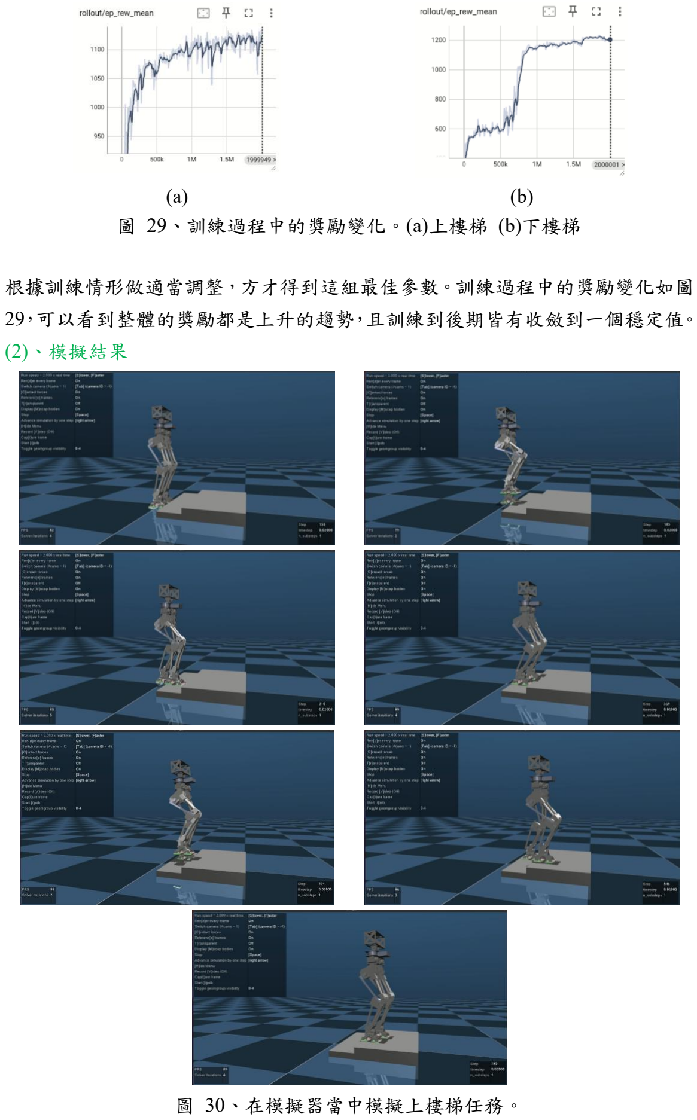
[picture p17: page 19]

(a) (b)
圖 29、訓練過程中的獎勵變化。(a)上樓梯 (b)下樓梯

根據訓練情形做適當調整，方才得到這組最佳參數。訓練過程中的獎勵變化如圖 29，可以看到整體的獎勵都是上升的趨勢，且訓練到後期皆有收斂到一個穩定值。 (2)、模擬結果

圖 30、在模擬器當中模擬上樓梯任務。

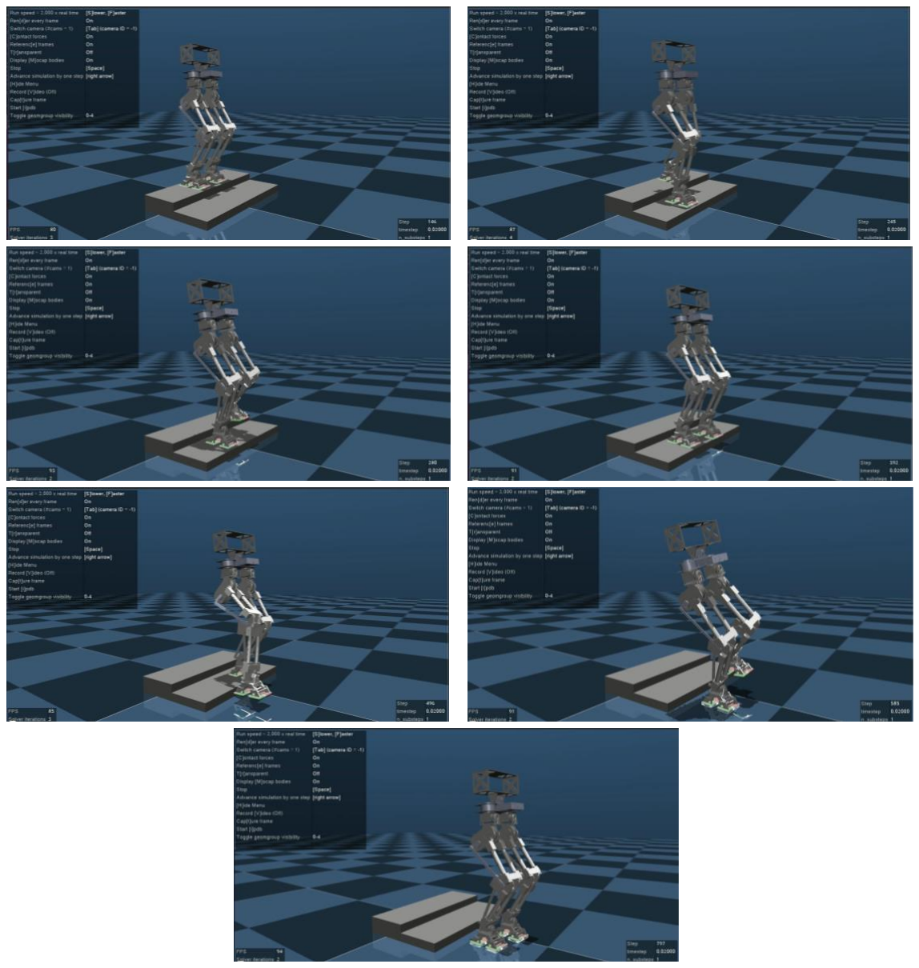
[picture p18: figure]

圖 31、在模擬器當中模擬下樓梯任務。

3. 行走於不平坦地形
A. 簡介
一個穩定的步態可以使機器人順利的在平面上行走。然而在實際的環境中， 機器人將受到不同程度外界的影響，地面可能會有些微起伏，也可能有微小障礙 物的存在，這些情況都會使機器人預期的行走產生偏差，進而導致跌倒。地面可 能會有輕微起伏，也可能有小障礙物。這些情況都會導致機器人的預期行走出現 偏差，進而導致摔倒。因此，在本任務的目標中，希望能讓機器人能夠抵銷上述 提及的干擾所造成的擾動，使其在不平坦地面仍能像平坦地面行走。 當機器人在凹凸不平的地面或有障礙物的表面上行走時，機器人的腳會與地 面接觸並產生一定的角度。如果傾斜角向上，機器人會按照原來的步態向後倒下； 同樣，如果傾斜角向下，機器人會向前倒下。透過對各個關節進行軌跡的重新計

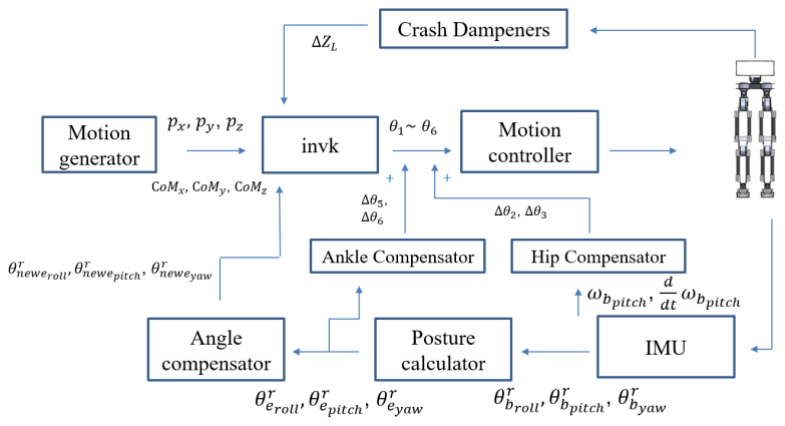
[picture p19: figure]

算以及補償關節的角度，使其上方的關節能讓 CoM（質量中心）保持在平面上 行走的姿勢。
圖 32 為不平坦地形實現的簡易架構圖。機器人首先會基於事先產生好的 LIPM 動作檔產生一連串的馬達角度去完成行走動作，接著機器人會透過獲取放 置在基座上 IMU 的角度姿態去進行末端點的角度計算以獲取地形的傾斜資訊， 並透過當前機器人軀幹的傾斜角度去對應適應的傾斜角度去進行微調，之後將更 新的資訊與走平地的步態去進行結合生成出新的適應當前地形的動作軌跡檔，以 橫越複雜地形。同時，對於適應未知地形中可能會造成的擾動，如為了減少地面 的衝擊而使用了碰撞緩衝器，以及髖關節與腳踝關節的角度補償，亦與主要方法 一起結合，獲得有效的成果。
B. 地形偵測
實際的地形千變萬化，各種類型的場景無法一一舉例，但可以先以簡單的方 式對其進行簡化分析，如圖 33 所示。從圖中可以看到，腳踩上的地面為兩個不 同的地形障礙物，然而腳的擺放位置與角度卻十分相近，因此可以將這兩種地形 視為同一種狀態。腳的旋轉方向可以分為 3 個自由度，分別為沿著縱軸旋轉的 roll 方向、沿著橫軸旋轉的 pitch 方向以及沿著槌軸旋轉的 yaw 方向。由於這三 個自由度互相垂直的關係，可以視為互不干擾，所以可以對其進行分解分開計算 再合併。

圖 33、地形示意圖

圖 32、不平坦地形對策架構圖

為了能對適應不同的地形，需要去偵測當前腳底板對於世界坐標系的姿態， 而腳底板的姿態可以經由放置在基座上的 IMU 去推算。首先需要將 IMU 所測量 到的 roll、pitch 和 yaw 方向角轉換成旋轉矩陣：

Rb = Rb_yaw(φ)Rb_pitcℎ

(θ)Rb_roll(φ)

= [

C θ Cφ Sφ S θ C φ − Cφ Sφ Cφ S θ C φ + Sφ Sφ C θ sin φ Sφ S θ Sφ + C φ Cφ Cφ S θ S φ − S φ Cφ
−S θ | Sφ C θ | cos φ C θ

] ，
(44)

其中R右下標的 b 代表 base(基座)的旋轉矩陣，C θ代表cos θ、S θ代表sin θ，其他 以此類推。機器人腿部以機器人 base 為坐標軸原點的機器人坐標系的末端座標 和旋轉矩陣可透過機器人每個馬達關節的角度得出：

HE

0 = H1

0H2

1H3

2H4

3H5

4H6

5HE

6 = PE

0 = [

r11 | r12 | r13
r21 | r22 | r23
r31 | r32 | r33

P0E,x

P0E,y

P0E,z
0 0 0 1

] ，

where Re = [

r11 | r12 | r13
r21 | r22 | r23
r31 | r32 | r33

]，

(45)

其中，Re是末端點相對於基座的旋轉矩陣，將兩個旋轉矩陣相乘來獲得末端點在 世界坐標系的旋轉矩陣，然後透過式(46)-(49)計算出末端點在世界坐標系中roll、 yaw、pitch 三個方向的角度，即可得出末端點的當前姿態。

Rbe = ReRb | (46)
θeroll = tan⁻¹ (
r32

be
r33
be) | (47)

θepitcℎ = tan⁻¹
(

−r31

be
√r32
be2
+ r33

be2

)

(48)

θeyaw = tan⁻¹ (
r21

be
r11
be) | (49)
C. 穩定補償

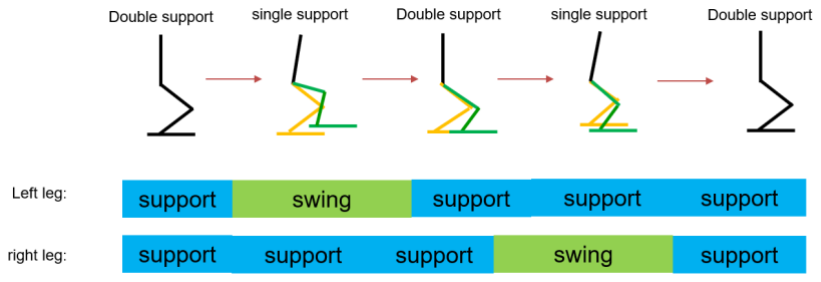
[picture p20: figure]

圖 34、行走週期

機器人行走二步的週期如圖 34 所示，可以看出機器人的左右腿分別會經過 support(支撐腳)以及 swing(擺動腳)的階段。當機器人所屬在未知的環境中，其 對接下來的地形是未知的，因此其會採取行走在平地上的步態軌跡。從圖中可 以看出，若是前方地面為起伏地形時，當機器人從 single support 轉換為 double support 時，擺動腳將會接觸到地面，並造成機器人的不穩定。為了檢測擺動腳 何時碰觸到地面，可以使用安裝在腳底板上的壓力感測器去偵測。一旦壓力感 測器偵測到數值，即可立即去計算末端點的姿態，以便之後能及時去重新規劃 行走的軌跡，使其能符合當前接觸的地形。
在重新規劃軌跡之前，機器人即有可能就因為突如其來的接觸而造成跌倒， 因此需要另外使用一連串的策略去進行平衡補償。設機器人的行走一步的週期為 T，雙腳支撐時間的比例為 kdsp(即圖 34 中擺動的那隻腳在一步中支撐地面時間 的比例)，則即可推算出正常平地行走中，機器人擺動腳落地的期望時間t2 = T −

k dsP
2 ，透過偵測壓力感測器讀到數值的時間與落地期望時間的對比，可以判斷出

下一步地面相對於前一步位置的水平高低以利於反應應對。此外，由於壓力感測 器平均的分佈在腳底的四個端點，可以透過先讀取到哪一個值去推測判斷當前的 地形，如腳尖分布的壓力感測器先讀值則極可能代表當前的地勢偏向上坡，此時 即可對機器人的腳踝角度進行事先補償，盡可能地讓腳底能快速貼平地面，以便 盡快掌握當前的地形資訊。
∆θ5 = k1 (
1
1 + e

−θepitcℎ

−

1
2
)， | (50)

∆θ6 = k2 (

1
1 + e

−θeroll

−

1
2
)。 | (51)

式(50)-(51)計算了需要去補償的腳踝角度，∆θ5和∆θ6分別為需要去快速適應的 pitch 和 roll 方向的補償變化量，k1和k2為增益的係數。 距離機器人的軀幹最近的關節為髖關節，其離末端點的距離相對於其他關節 馬達的距離也最遠，造成的力矩也會相對較大，因此髖關節的角度變動對於機器 人的重心轉移會有明顯的影響。當我們在讓腳踝快速適應地面時，可能會造成機 器人的不穩定，此時就須要對髖關節的角度進行相對應的補償，其相關式子如式

(52)-(53)所示:

∆θ3 = G1ωbpitcℎ + G2

d
dt ωbpitcℎ， | (52)

∆θ2 = G3ωbroll + G4

d
dt ωbroll。 | (53)

其中，ωb為機器人基座上的角速度，d
dt

ωb為基座上的角加速度，G1~G4為比例係

數。突然的角速度或角加速度變化可能會導致失去平衡，透過對這些狀態去做偵 測，可以預測機器人重心偏移方向，進而去做補救的措施。

由於機器人行走時我們給定的是各個關節的馬達應旋轉的角度，故在擺動腳 接觸到地面時會產生很大的衝擊，此衝擊不但會造成機器人行走的不穩定，同時 也會對馬達造成程度不一的磨損，進而加速減少其使用壽命。因此，需要對這部 分進行緩衝處理使其著陸更加柔順。我們在接別人丟過來的球時，會將手向後彎 曲以便吸收並緩衝衝擊，同理，我們可以將此想法應用到機器人身上，在腳與地 面接觸時，透過動態的調整腳的高度，在高衝擊時將其略為彎曲以緩衝地面造成 的反作用力。

∆ZL = k3fL， | (54)
∆ZR = k3fR， | (55)
其中∆Z為彎曲所減少的腳長度，下標的L和R分別表示左腳和右腳，f為下標所屬 的腳四個壓力感測器的合力值，而k3為增益係數。接著將計算出的變化量∆Z套入 逆向運動學進行計算，即可獲得更新後的θ3、θ4、θ5。 最後，對於獲取的末端點的姿態，將對其進行基於基座角度的微調。由於原 始的步態是依據平地去產生的，因此儘管將其軌跡去適應地形的起伏，仍然會有 一些誤差。透過追蹤實際與期望的基座角度變化，可以獲得最適合的姿態角度。

θnewepitcℎ = θepitcℎ + k4 ∙ (θbpitcℎ
d | − θbpitcℎ

r

) ， | (56)

θneweroll = θeroll + k5 ∙ (θbroll

d − θbroll

r
)， | (57)
其中式(54)表示的是 pitch 方向的調整，式(55)則為 roll 方向的調整。θ右上標的d 表示為期望的基座角度，θ右上標的r表示為實際的基座角度，k4以及k5為增益參 數，可以透過智慧型演算法去尋找最佳解。
D. 模擬展示

對於機器人在不同的地形中進行行走在模擬中進行了一些測試，下面分成幾 個不同的場景分別測驗各種情況下的結果。
(1)、不連續地面
圖 35 顯示了機器人走下高度約 1.2 公分的不連續地面。從圖 36 以及圖 37 中可 以看出，一開始的馬達角度與走平地時無異，然而當腳在接觸到地面的時候， 由於與期望的平地地形產生誤差，因此機器人能快速的針對地形的起伏去作出 調整，馬達的軌跡角度也開始與平地的步態出現差異。最後機器人能成功地走 下地面。

圖 35、不連續地面

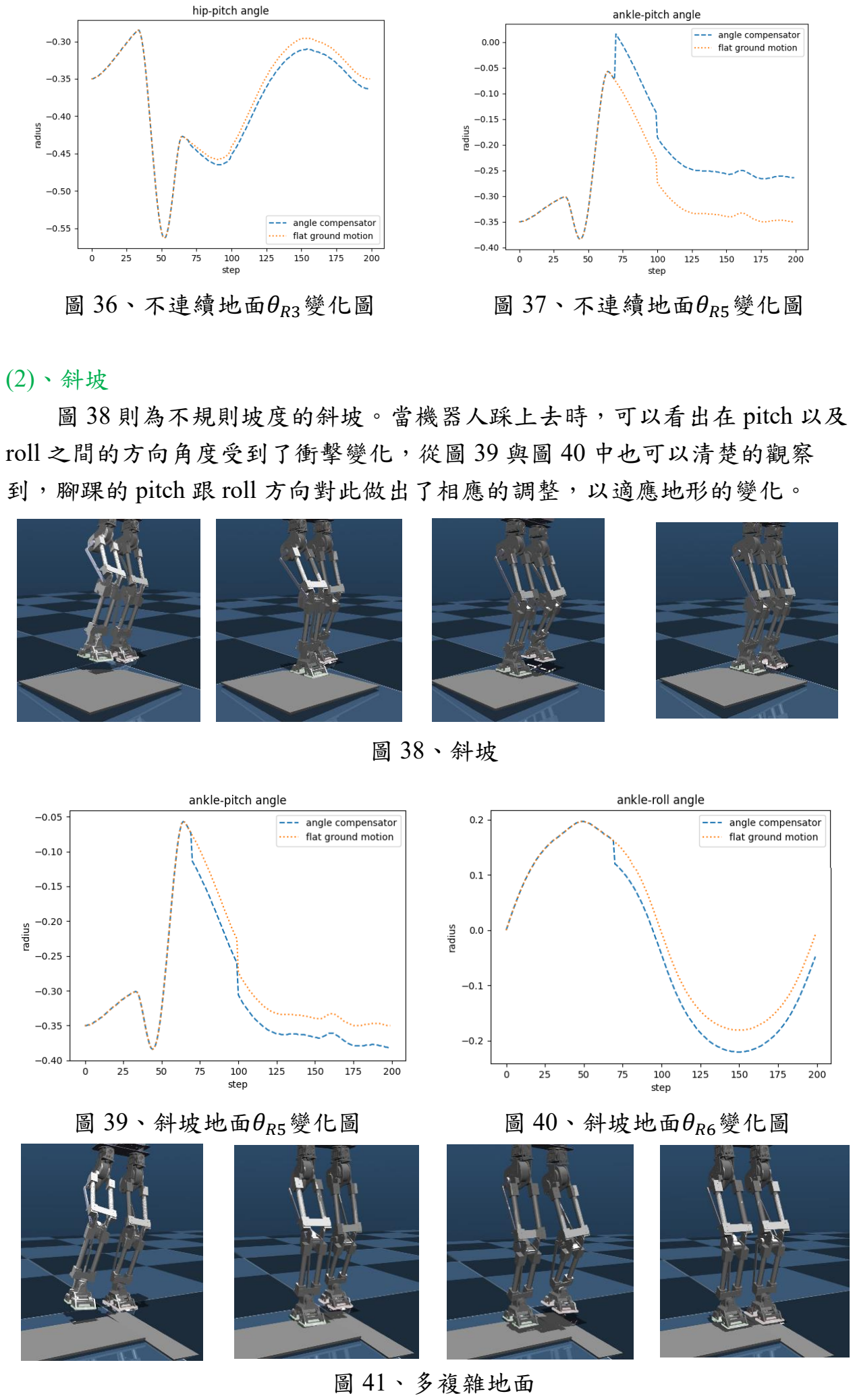
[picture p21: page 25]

圖 36、不連續地面θR3變化圖 | 圖 37、不連續地面θR5變化圖

(2)、斜坡
圖 38 則為不規則坡度的斜坡。當機器人踩上去時，可以看出在 pitch 以及 roll 之間的方向角度受到了衝擊變化，從圖 39 與圖 40 中也可以清楚的觀察 到，腳踝的 pitch 跟 roll 方向對此做出了相應的調整，以適應地形的變化。

圖 38、斜坡

圖 39、斜坡地面θR5變化圖 | 圖 40、斜坡地面θR6變化圖

圖 41、多複雜地面

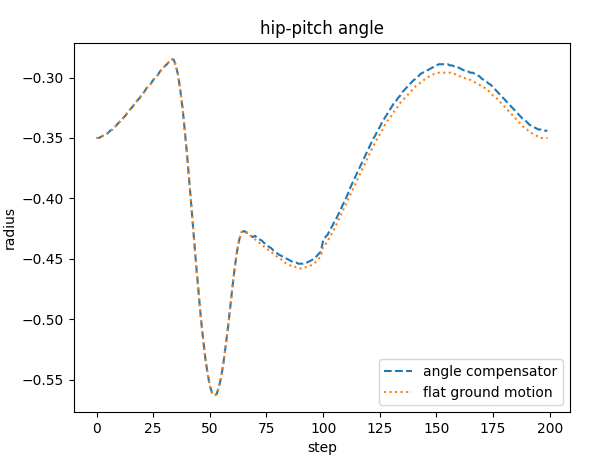
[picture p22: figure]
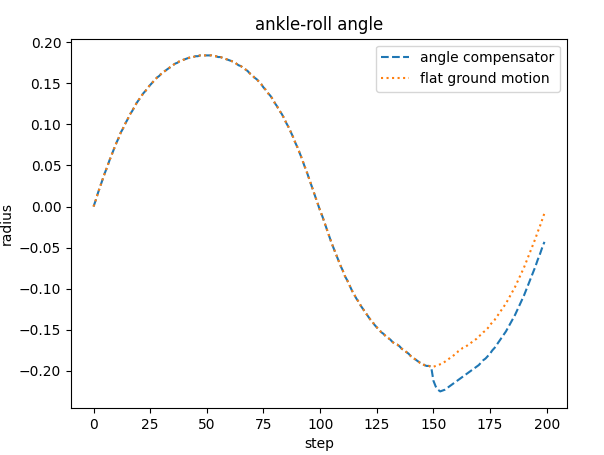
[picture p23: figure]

圖 42、多複雜地面θR3變化圖 | 圖 43、多複雜地面θL6變化圖
(3)、多複雜地面
最後則為左右兩腳將踩上兩種傾斜幅度不一樣的地形，其流程的截圖如圖 41 所示。除了與前面的結果呈現的一樣機器人有針對地形改變腳的擺動軌跡之 外，可以看到圖 43 顯示的是右腳腳踝的整體軌跡，由於左腳比較晚接觸到變化 的地面，因此角度改變的時間點也比較後面，最後機器人也能成功走上複雜的 地面。

五、實體實驗

經由 MuJoCo [15]模擬軟體驗證步態之穩定性及可行性後，本作品設計了實 體雙足型機器人的三種實驗場景，一一分述如下:

實驗一、負重行走實現

雙足機器人在倉儲環境的運送任務中，負重對機器人來說是一大挑戰，這裡 所謂負重是足以改變機器人重心的重量，並且運送的貨品是無法確認重量的， 因此機器人必須要有自適應能力將重心調整回適當位置，以利於接下來的運送 任務。這次的運送任務如圖 45，機器人所要運送的貨品為 2 kg 如圖 44，這個 重量是為此機器人重量的十分之一，對人來說身體重量的十分之一是個具有負 擔的重量。
此次運送任務中，圖 46 至圖 49 前 200 筆數據為機器人從站直到平衡階 段，可以看到雙足機器人在被賦予貨品時質心傾斜且零力矩點偏移，通過平衡 控制器以及負重策略使機器人在約 350 個時間步長後回到穩定狀態。穩定後機 器人開始運用動態的平衡控制器，使其在運動過程中保持穩定，質心角速度的 絕對值也幾乎未超過設定的閥值，由此可以看到此控制系統之強健性。

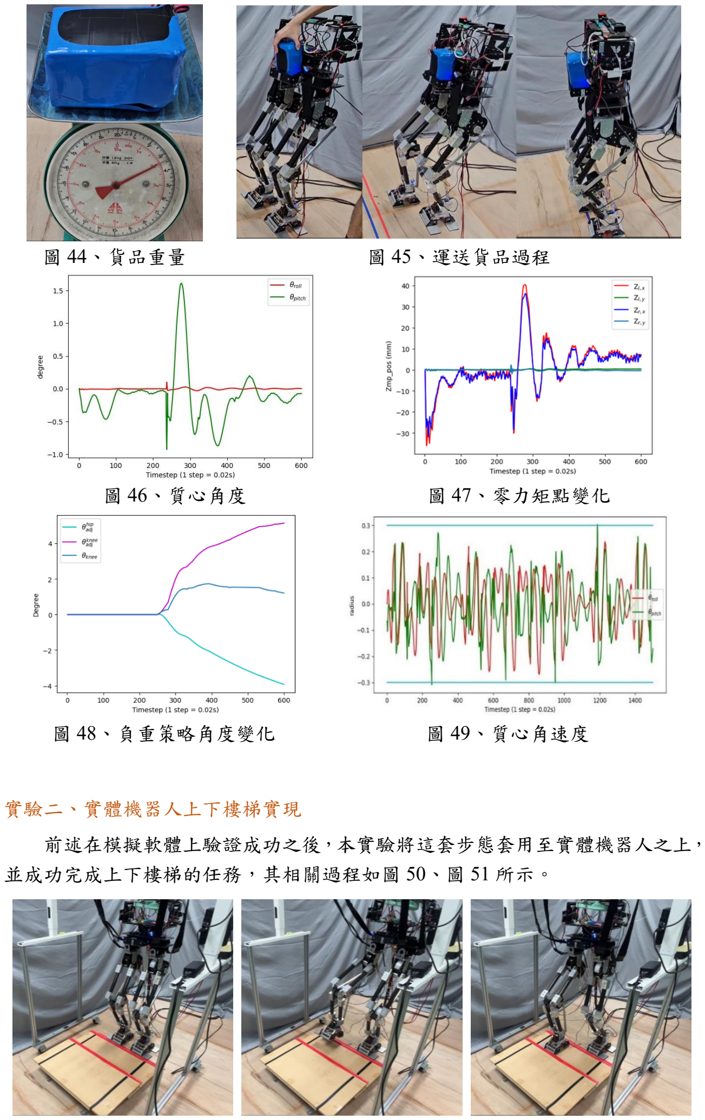
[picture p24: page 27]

圖 44、貨品重量 | 圖 45、運送貨品過程
圖 46、質心角度 | 圖 47、零力矩點變化
圖 48、負重策略角度變化 | 圖 49、質心角速度

實驗二、實體機器人上下樓梯實現

前述在模擬軟體上驗證成功之後，本實驗將這套步態套用至實體機器人之上， 並成功完成上下樓梯的任務，其相關過程如圖 50、圖 51 所示。


圖 50、實體上樓梯

圖 51、實體下樓梯

圖 52、不平坦地形行走


實驗三、不平坦地形的橫越

第三部份讓機器人嘗試行走在不規則的地面上。如圖 52 可以看到機器人的 前方有數塊木片以不同的方向堆積起來，使得每一步地行走遇到的起伏都會不同。 然而機器人能夠透過感知地形的變化去適應並產生出新的符合當前狀況的步行 軌跡，最後成功地度過障礙。

七、結論

本企劃實現了人型機器人下半身機構和系統結構的創新設計，以及實體的組 裝和測試。腿部設計的目標是實現輕量化，並模仿人類腿部結構，使雙足機器人 的質心向上移動，從而減少轉動慣量。其中，我們採用了特殊的四連桿機構設計， 使機器人的重心能夠更接近人類。關於腳板的設計，為了減少與環境互動時的振 動，該機構模仿了人腳的足弓。此外，在前腳趾和後腳跟部分使用了可旋轉的被 動關節。
在操作的層面中，我們讓機器人在行走前能夠先進行平衡，確保一開始的穩 定性。除了能夠正常地行走之外，我們的機器人還能更進一步突破許多地形限制， 如走樓梯或是不平坦的地形等，使機器人執行任務的層面上能夠更加靈活。

八、參考資料

[1] | A. | Robotics. | “Made | for | Work, | ” | 30 | Mar., | 2024;

https://www.youtube.com/watch?v=Jycdks836bY.

[2] B. Dynamics. “ATLAS™ Atlas is a research platform designed to push the limits of

whole-body mobility," 31 Mar., 2024; https://bostondynamics.com/atlas/.

[3] | Tesla. | “Optimus | - | Gen | 2, | ” | 01 | Apr., | 2024;

https://www.youtube.com/watch?v=cpraXaw7dyc.

[4] M. Xsens. 02 Apr., 2024; https://www.movella.com/products/xsens.
[5] | 廣 華 電 子 商 城 . | " 薄 膜 壓 力 傳 感 器 ," | 02 Apr., | 2024;

https://shop.cpu.com.tw/product/56021/print/.

[6] J. Kennedy, and R. Eberhart, “Particle swarm optimization. ” pp. 1942-1948 vol.4.
[7] S. Fujimoto, H. Hoof, and D. Meger, “Addressing function approximation error in

actor-critic methods. ” pp. 1587-1596.

[8] | J. | Achiam. | “Twin | Delayed | DDPG, | ” | 30 | Mar., | 2024;

https://spinningup.openai.com/en/latest/algorithms/td3.html.

[9] D. Manzoni, “Vestibulo-spinal Reflexes, ” Encyclopedia of Neuroscience, M. D. Binder,
N. Hirokawa and U. Windhorst, eds., pp. 4245-4250, Berlin, Heidelberg: Springer

Berlin Heidelberg, 2009.

[10] T.-H. S. Li, Y.-F. Ho, P.-H. Kuo, Y.-T. Ye, and L.-F. Wu, “Natural Walking Reference

Generation Based on Double-Link LIPM Gait Planning Algorithm,” IEEE Access, vol.

5, pp. 2459-2469, 2017.

[11] C. Liu, W. Geng, M. Liu, and Q. Chen, “Workspace Trajectory Generation Method for

Humanoid Adaptive Walking With Dynamic Motion Primitives,” IEEE Access, vol. 8,

pp. 54652-54662, 2020.

[12] V. Mnih, K. Kavukcuoglu, D. Silver, A. A. Rusu, J. Veness, M. G. Bellemare, A. Graves,
M. Riedmiller, A. K. Fidjeland, G. Ostrovski, S. Petersen, C. Beattie, A. Sadik, I.

Antonoglou, H. King, D. Kumaran, D. Wierstra, S. Legg, and D. Hassabis, “Human-

level control through deep reinforcement learning,” Nature, vol. 518, no. 7540, pp. 529-

33, Feb 26, 2015.

[13] J. Schulman, F. Wolski, P. Dhariwal, A. Radford, and O. Klimov, “Proximal policy

optimization algorithms,” arXiv preprint arXiv:1707.06347, 2017.

[14] D. Silver, G. Lever, N. Heess, T. Degris, D. Wierstra, and M. Riedmiller, “Deterministic

Policy Gradient Algorithms,” 31st International Conference on Machine Learning,

ICML 2014, vol. 1, 06/21, 2014.

[15] E. Todorov, T. Erez, and Y. Tassa, “MuJoCo: A physics engine for model-based control,”

in 2012 IEEE/RSJ International Conference on Intelligent Robots and Systems, 2012,

pp. 5026-5033.

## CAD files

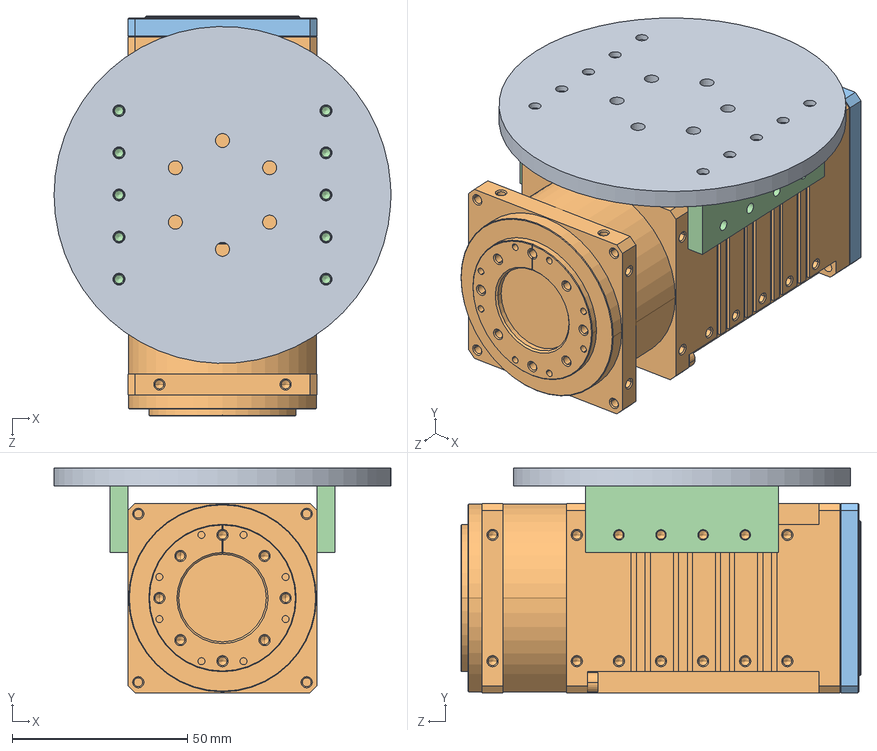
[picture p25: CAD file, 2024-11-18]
Humanoid Robot Mechanism/30_40_Hip/30_40_Hip.SLDASM
96.0 x 64.0 x 114.0 mm
30_40_Hip_disk_YAS
H54P-100_M54P-040
dinamixel-100 sub-turntabl
30_40_Hip_fixation_board x 2

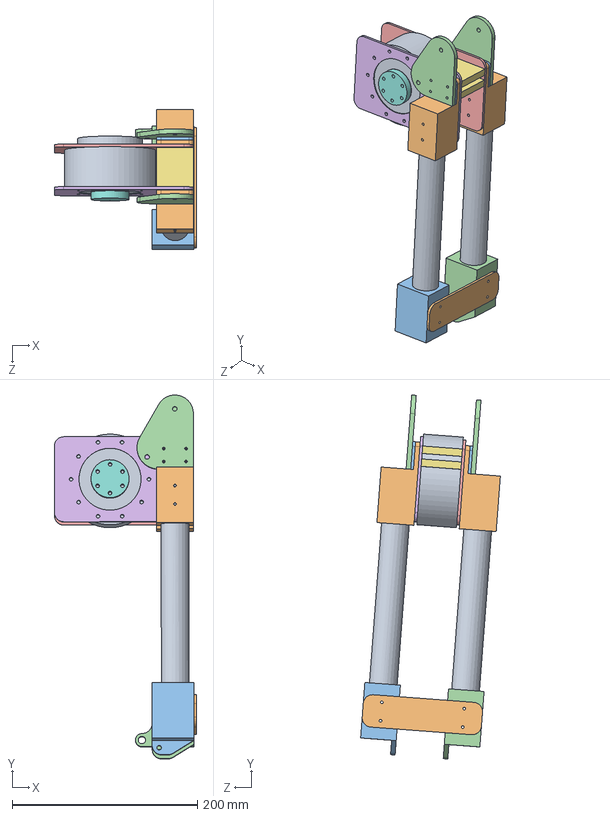
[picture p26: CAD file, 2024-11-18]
Humanoid Robot Mechanism/left_foot/left foot_578.SLDASM
153.4 x 392.6 x 150.7 mm
RMD-X8-S2-V3-Model
tibia-bone sleeve upward x 2
knee cushion x 2
knee linkage x 2
knee-external fixation board
knee-internal fixation board
knee x 2
ankle-motor cushion
tibia x 2
bone connection bottom
tibia-bone sleeve bottom(R)
tibia-bone sleeve bottom damp(L)

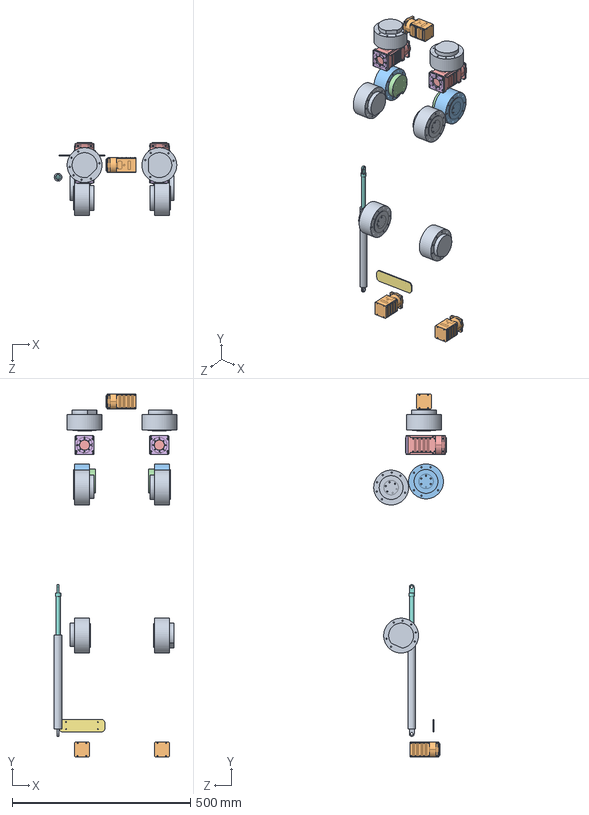
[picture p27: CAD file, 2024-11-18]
Humanoid Robot Mechanism/lower_body1.SLDASM
344.2 x 1019.4 x 204.0 mm
RMD-X8-S2-V3-Model x 6
H42P-020-S300-R x 3
motor front x 2
motor back x 2
H54P-100_M54P-040 x 2
dinamixel-100 sub-turntabl x 2

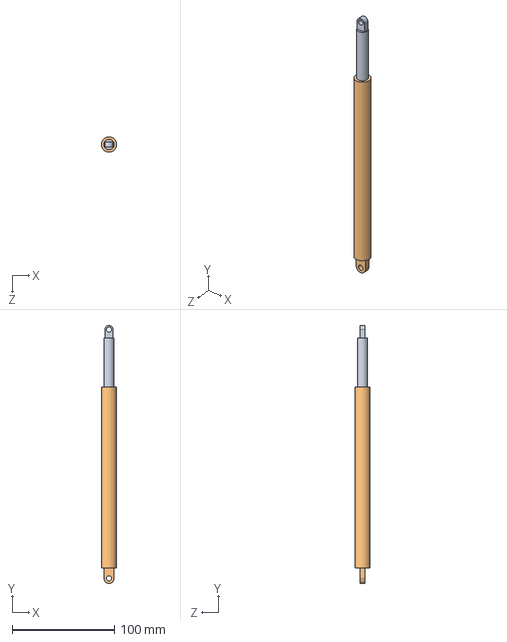
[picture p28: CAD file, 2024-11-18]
Humanoid Robot Mechanism/right_foot/right foot_8.SLDASM
15.0 x 252.0 x 15.0 mm
damper rod
Damper sleeve

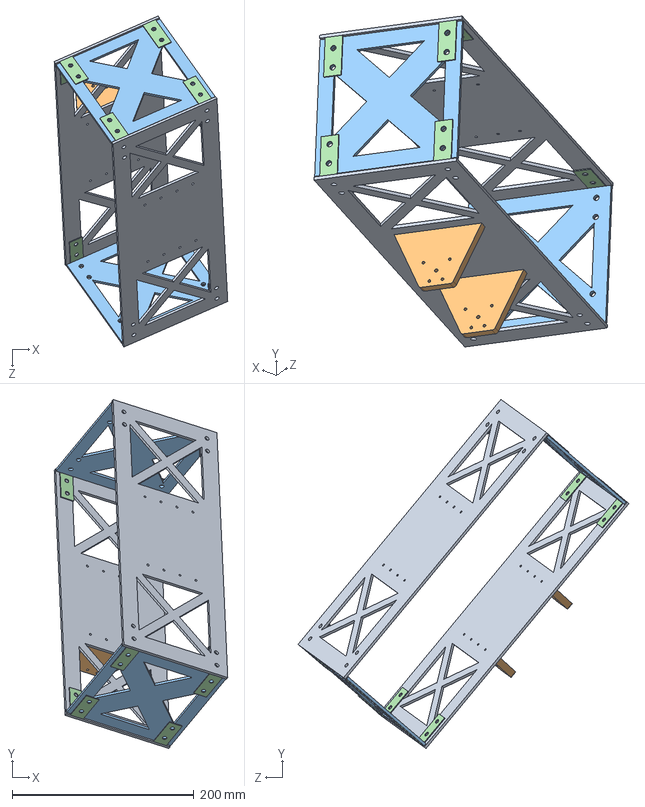
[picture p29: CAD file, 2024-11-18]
Humanoid Robot Mechanism/trunk/trunk.SLDASM
190.9 x 383.8 x 364.0 mm
trunk_bottom x 2
trunk_connector x 2
trunk_side_panel x 2
L fixation x 8

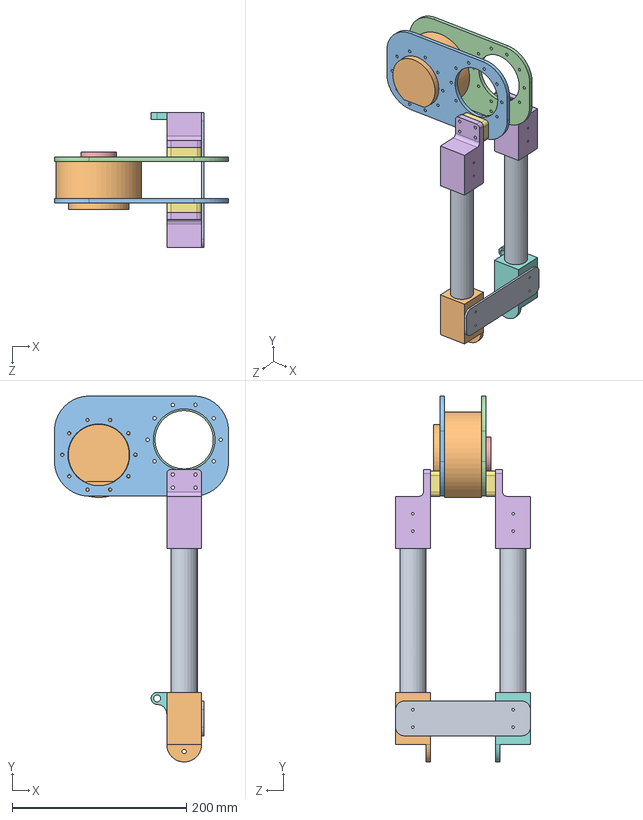
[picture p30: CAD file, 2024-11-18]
Humanoid Robot Mechanism/left_foot/left foot_2.SLDASM
200.0 x 420.2 x 155.0 mm
thigh bone x 2
RMD-X8-S2-V3-Model
thigh-internal fixation board
thigh-external fixation board
tibia-motor cushion
thigh-bone sleeve upward x 2
hip cushion x 2
tibia-bone sleeve damper left
bone connection upward
thigh bone sleeve bottom

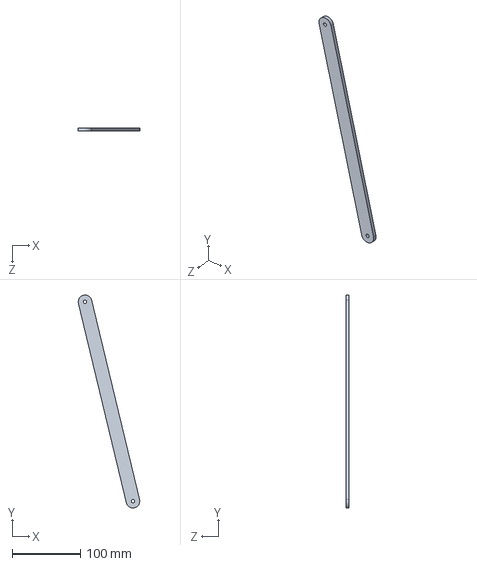
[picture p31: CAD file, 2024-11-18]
Humanoid Robot Mechanism/right_foot/right foot_10.SLDASM
90.0 x 311.1 x 5.00 mm

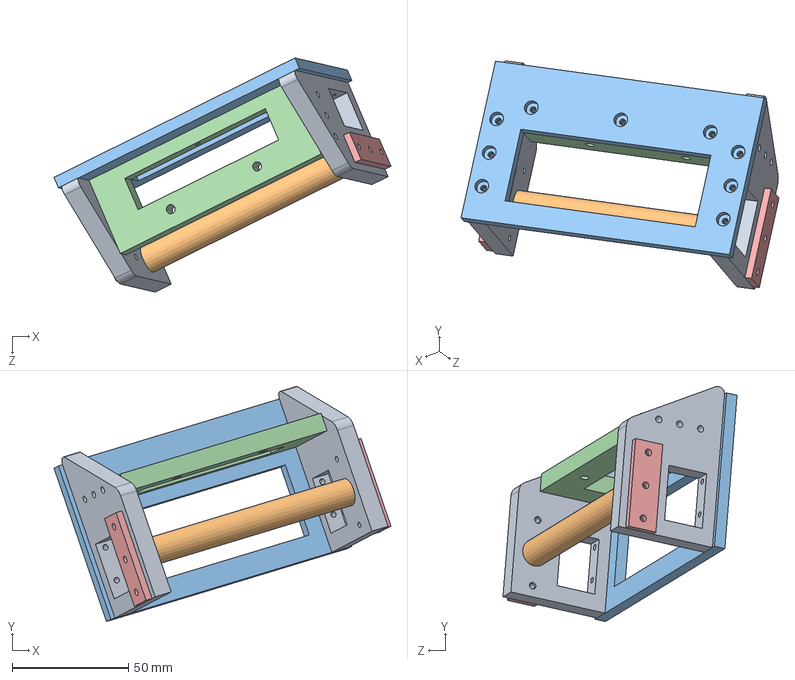
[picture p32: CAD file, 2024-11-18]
Humanoid Robot Mechanism/Footplate_new/link_1.SLDASM
145.1 x 101.3 x 100.8 mm
Trapezoidal_side_panels x 2
Trapezoidal_axis
Trapezoidal_base_plate
Torque spring front fender
Rotating shaft holder x 2

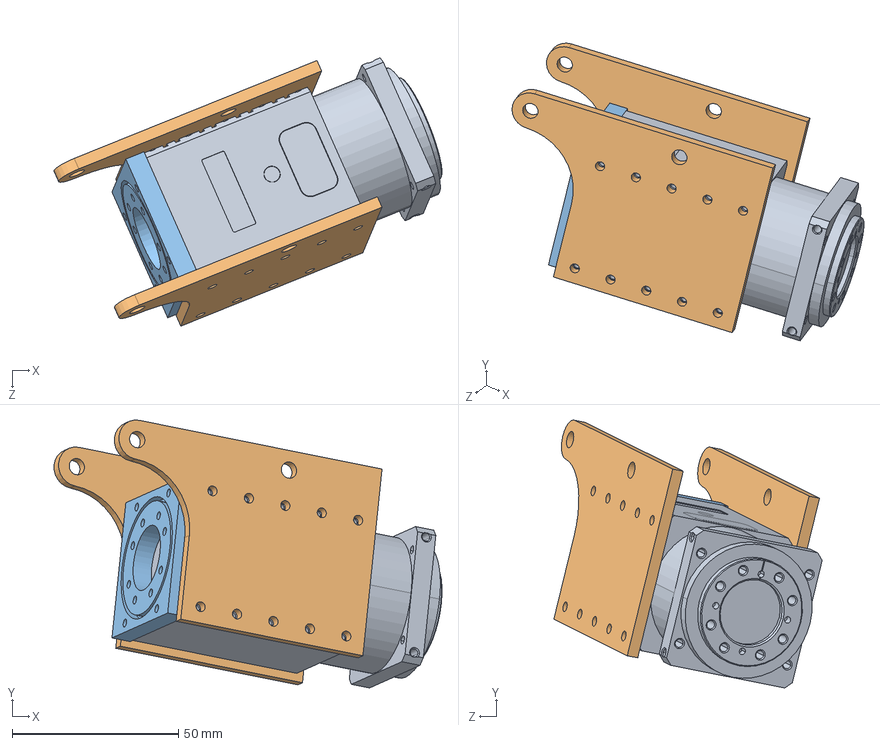
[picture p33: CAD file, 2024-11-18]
Humanoid Robot Mechanism/left_foot/left foot_1112.SLDASM
116.6 x 80.5 x 80.6 mm
H42P-020-S300-R
ankle linkage x 2
Motor_sub_turntable_H4-20-S300-R

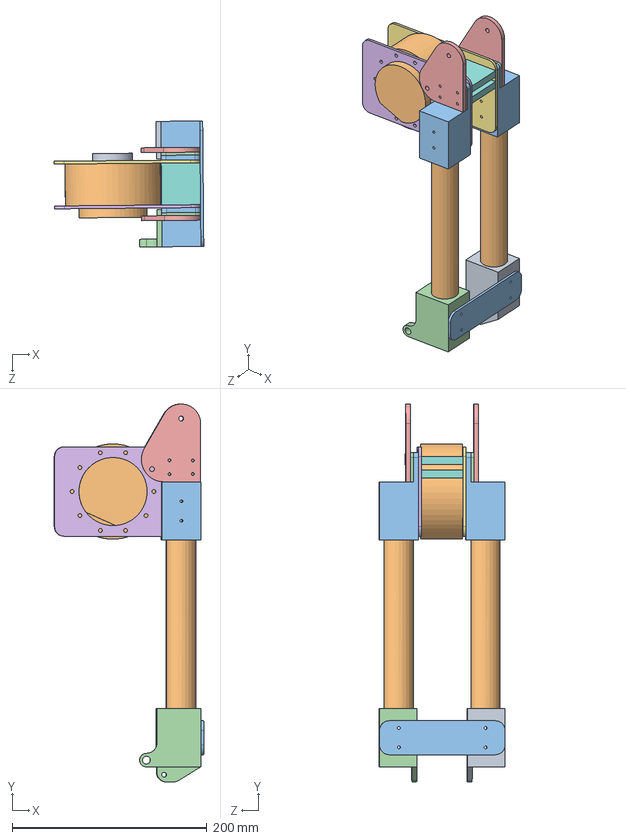
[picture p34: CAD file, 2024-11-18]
Humanoid Robot Mechanism/right_foot/right foot_578.SLDASM
153.8 x 388.5 x 129.6 mm
tibia-bone sleeve bottom(L)
RMD-X8-S2-V3-Model
tibia-bone sleeve upward x 2
knee cushion x 2
knee linkage x 2
knee-external fixation board
knee-internal fixation board
knee x 2
ankle-motor cushion
tibia x 2
bone connection bottom
tibia-bone sleeve bottom damp(R)

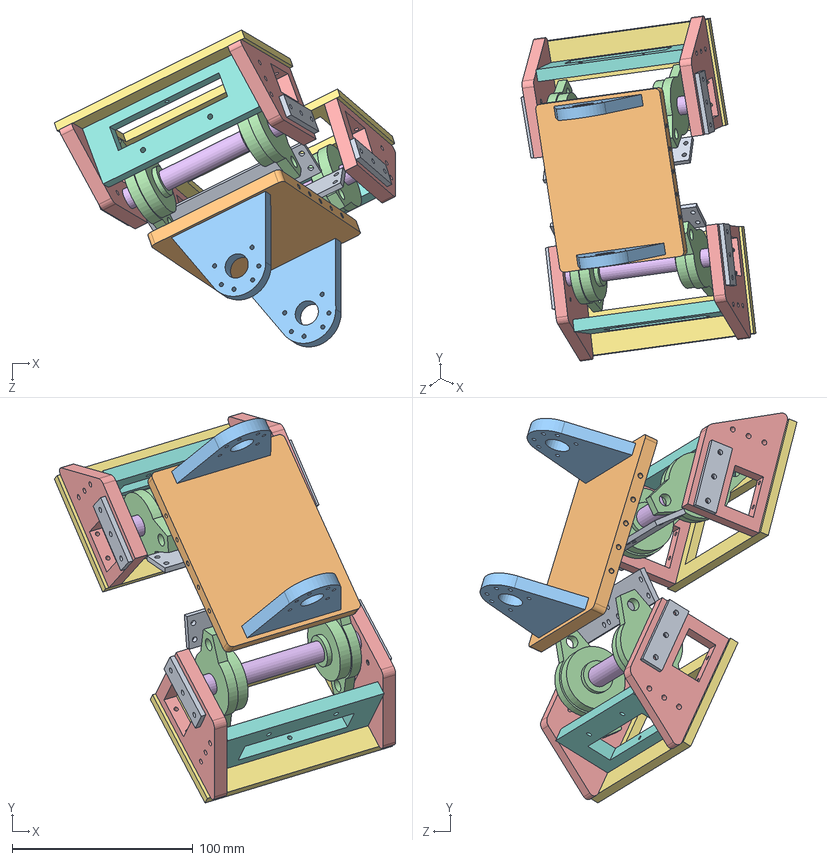
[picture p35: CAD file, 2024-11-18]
Humanoid Robot Mechanism/Footplate_new/Footplate_new.SLDASM
189.1 x 216.0 x 175.5 mm
Spring_baffle x 2
Motor_base_plate
Front_side_connection_of_motor x 2
bearing x 4
Trapezoidal_side_panels x 4
Trapezoidal_axis x 2
Trapezoidal_base_plate x 2
Torque spring front fender x 2
Rotating shaft holder x 4

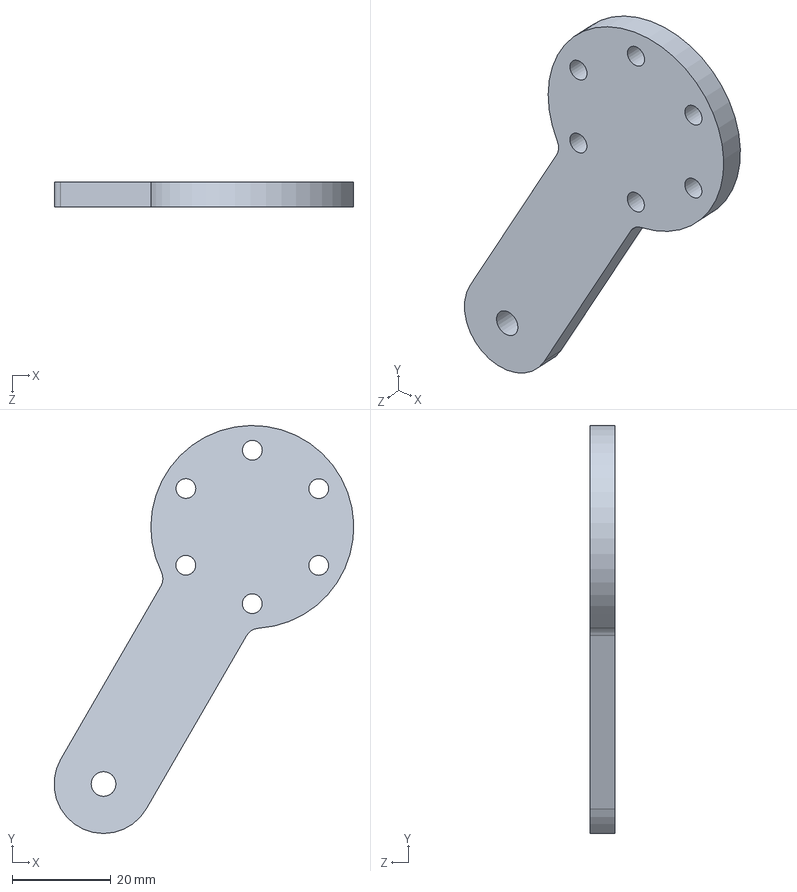
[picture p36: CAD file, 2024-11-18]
Humanoid Robot Mechanism/left_foot/left foot_3.SLDASM
60.5 x 82.4 x 5.00 mm

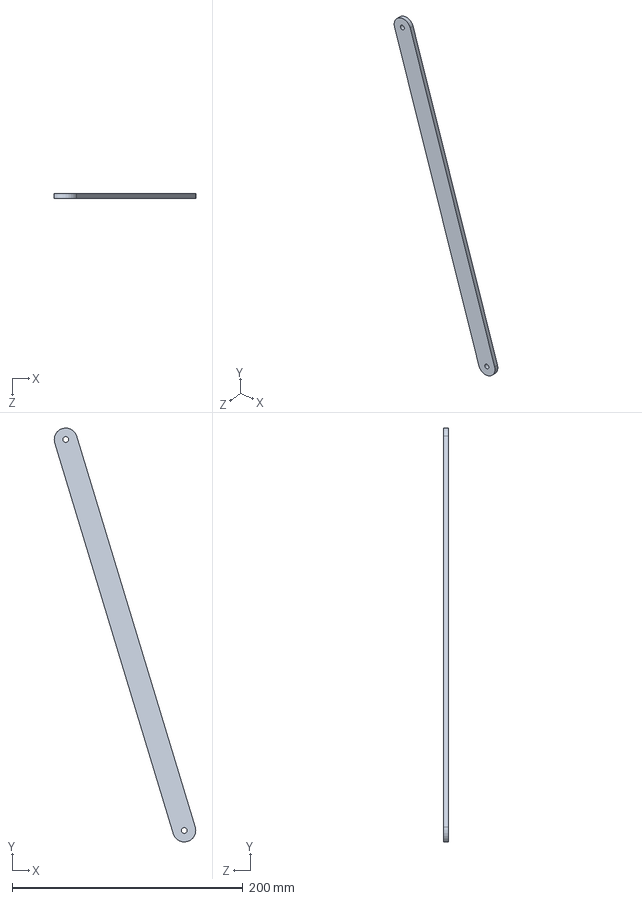
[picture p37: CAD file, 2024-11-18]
Humanoid Robot Mechanism/right_foot/right foot_4.SLDASM
122.9 x 359.2 x 4.50 mm

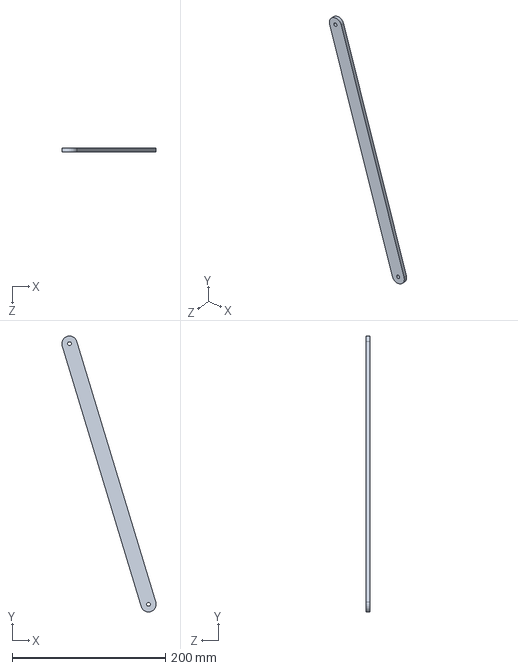
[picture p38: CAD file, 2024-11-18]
Humanoid Robot Mechanism/left_foot/left foot_4.SLDASM
123.0 x 359.8 x 5.00 mm

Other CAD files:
Humanoid Robot Mechanism/right_foot/right foot_6-1.SLDASM
Humanoid Robot Mechanism/left_foot/left foot_10.SLDASM
Humanoid Robot Mechanism/right_foot/right foot_6-2.SLDASM
Humanoid Robot Mechanism/Hip/right Hip.SLDASM
Humanoid Robot Mechanism/30_40_Hip/30_40_Hip_disk_YAS.SLDPRT
Humanoid Robot Mechanism/30_40_Hip/30_40_Hip_fixation_board.SLDPRT
Humanoid Robot Mechanism/30_40_Hip/H54P-100_M54P-040.SLDPRT
Humanoid Robot Mechanism/30_40_Hip/dinamixel-100 sub-turntabl.SLDPRT
Humanoid Robot Mechanism/Feet/FRP42-I110K.SLDPRT
Humanoid Robot Mechanism/Feet/H42P-020-S300-R.SLDPRT
Humanoid Robot Mechanism/Feet/RMD-X8-S2-V3-Model.SLDPRT
Humanoid Robot Mechanism/Feet/ankle linkage.SLDPRT
Humanoid Robot Mechanism/Feet/ankle-linkage driver.SLDPRT
Humanoid Robot Mechanism/Feet/ankle-motor cushion.SLDPRT
Humanoid Robot Mechanism/Feet/bone connection bottom.SLDPRT
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

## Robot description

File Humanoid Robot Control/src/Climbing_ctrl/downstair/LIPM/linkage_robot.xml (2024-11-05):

<mujoco model="smallwhitechi">
    <compiler angle="radian" meshdir="C:/Users/poetr/Desktop/Roli/Linkage_Robot_simulation-master/linkage_robot/meshes" />
    <size njmax="500" nconmax="100" />
    <option gravity = "0 0 -9.81" timestep="0.02"/>
    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
    <worldbody>
        <light directional="true" diffuse=".4 .4 .4" specular="0.1 0.1 0.1" pos="0 0 5.0" dir="0 0 -1" castshadow="false" />
        <light directional="true" diffuse=".6 .6 .6" specular="0.2 0.2 0.2" pos="0 0 4" dir="0 0 -1" />
        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
        <body name="base" pos="0 0 1.0301" >
        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
            <freejoint name="base" /> 
            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
            <body name="trunk" pos="0 0.00025 0.0585" quat="0.707107 -0.707107 0 0">
                <inertial pos="5.1972e-10 -0.0984798 0" quat="0.707107 0 0 0.707107" mass="0.645032" diaginertia="0.00413623 0.00355034 0.00103793" />
                <joint name="trunk" pos="0 0 0" axis="0 0 1" frictionloss="1000"/>
                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
            </body>
            <body name="L_hip_yaw" pos="0 0.105 0">
                <inertial pos="0.00391746 4.63721e-11 -0.0616421" quat="0 0.707025 0 0.707189" mass="0.840025" diaginertia="0.000921351 0.000895707 0.000373716" />
                <joint name="L_hip_yaw" pos="0 0 0" axis="0 0 1" frictionloss="1000"/>
                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
                <body name="L_hip_roll" pos="0 0 -0.064" quat="0.5 0.5 0.5 0.5">
                    <inertial pos="0.00526654 -0.0954491 0.00587283" quat="1 0 0 4.33964e-05" mass="1.07017" diaginertia="0.0011998 0.000809829 0.000756496" />
                    <joint name="L_hip_roll" pos="0 0 0" axis="0 0 1" frictionloss="1000"/>
                    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
                    <body name="L_hip_pitch" pos="0 -0.102 0.006" quat="0.5 -0.5 0.5 -0.5">
                        <inertial pos="0.09344 0.0500943 0.00650267" quat="0.0856942 0.702156 -0.0883782 0.701301" mass="2.02178" diaginertia="0.00307192 0.00206111 0.00179732" />
                        <joint name="L_hip_pitch" pos="0 0 0" axis="0 0 1" frictionloss="1000"/>
                        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
                        <body name="L3" pos="0.01728 0.098 0" quat="0 -1 0 0">
                            <inertial pos="0.0162353 -0.0093761 -0.042" quat="0.183054 0.683002 -0.183054 0.683002" mass="0.0325223" diaginertia="2.2109e-05 1.98014e-05 2.47162e-06" />
                            <joint name="L3" pos="0 0 0" axis="0 0 1" />
                            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
                            <body name="L4" pos="0.051958 -0.030006 -0.04425">
                                <inertial pos="0.170336 0.0490038 -0.00275" quat="-0.0987154 0.700182 0.0987154 0.700182" mass="0.089481" diaginertia="0.00101579 0.00101298 3.11705e-06" />
                                <joint name="L4" pos="0 0 0" axis="0 0 1" />
                                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
                            </body>
                        </body>

                        <body name="L8" pos="0.35795 0 0.00725">
                            <inertial pos="0.131559 0.0353145 0.00135098" quat="-0.00576963 0.707302 0.00236913 0.706884" mass="2.00878" diaginertia="0.00240461 0.00184281 0.00130688" />
                            <joint name="L8" pos="0 0 0" axis="0 0 1" frictionloss="1000" damping="1"/>
                            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
                            <body name="L_ankle_pitch" pos="0.366 0.0175 0" quat="0.999715 0 0 0.0238867">
                                <inertial pos="0.0269022 -0.0082598 -4.18233e-11" quat="0.49977 0.50023 -0.49977 0.50023" mass="0.463666" diaginertia="0.000310094 0.000280835 0.000128916" />
                                <joint name="L_ankle_pitch" pos="0 0 0" axis="0 0 1" frictionloss="1000" damping="1"/>
                                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
                                <body name="L_ankle_roll" pos="0.028967 -0.001385 0" quat="0.706904 0.706906 -0.0168905 -0.0168904">
                                    <inertial pos="0.0555093 -4.23772e-07 0.0180009" quat="0.999991 8.74188e-07 0.00433457 1.98489e-05" mass="0.707474" diaginertia="0.000681732 0.000625669 0.000245532" />
                                    <joint name="L_ankle_roll" pos="0 0 0" axis="0 0 1" frictionloss="1000"/>
                                    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
                                    <body name="L_f_front" pos="0.07175 0 0.072" quat="0.707105 0.707108 0 0">
                                        <inertial pos="0.0151668 0.0134538 -5.8362e-08" quat="0.999239 0 0 -0.0389993" mass="0.281294" diaginertia="0.000334027 0.000291577 7.55394e-05" />
                                        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
                                    </body>
                                    <body name="L_f_back" pos="0.07175 0 -0.028" quat="0.707105 -0.707108 0 0">
                                        <inertial pos="0.0151549 0.0134538 -5.8362e-08" quat="0.999236 0 0 -0.0390787" mass="0.281294" diaginertia="0.000334028 0.000291576 7.55394e-05" />
                                        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
                                    </body>
                                </body>
                            </body>
                            <body name="L9" pos="0.075 0.07 0" quat="-3.67321e-06 -1 0 0">
                                <inertial pos="-6.14218e-07 -0.0144143 0.0345" quat="0.500011 0.499989 -0.500011 0.499989" mass="0.0268657" diaginertia="1.44084e-05 1.23819e-05 2.13837e-06" />
                                <joint name="L9" pos="0 0 0" axis="0 0 1" />
                                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
                                <body name="L10" pos="0 -0.05 0.032" quat="1 0 0 -2.1306e-05">
                                    <inertial pos="0.1455 0.0262562 -0.0025" quat="-0.0630374 0.704291 0.0630374 0.704291" mass="0.08355" diaginertia="0.000671066 0.000668473 2.94056e-06" />
                                    <joint name="L10" pos="0 0 0" axis="0 0 1" />
                                    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
                                </body>
                            </body>
                        </body>
                    </body>
                </body>
            </body>
            <body name="R_hip_yaw" pos="0 -0.105 0">
                <inertial pos="0.00391746 4.65299e-11 -0.0616421" quat="0 0.707025 0 0.707189" mass="0.840025" diaginertia="0.000921351 0.000895707 0.000373716" />
                <joint name="R_hip_yaw" pos="0 0 0" axis="0 0 1" frictionloss="1000"/>
                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
                <body name="R_hip_roll" pos="0 0 -0.064" quat="0.5 0.5 0.5 0.5">
                    <inertial pos="-0.00526654 -0.0954491 0.00587284" quat="1 0 0 -4.33962e-05" mass="1.07017" diaginertia="0.0011998 0.000809829 0.000756496" />
                    <joint name="R_hip_roll" pos="0 0 0" axis="0 0 1" frictionloss="1000"/>
                    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
                    <body name="R_hip_pitch" pos="0 -0.102 0.006" quat="0.5 -0.5 0.5 -0.5">
                        <inertial pos="0.0934417 0.0501054 -0.00650267" quat="0.0872215 0.701411 -0.0849468 0.702281" mass="2.02178" diaginertia="0.00307192 0.00206097 0.00179747" />
                        <joint name="R_hip_pitch" pos="0 0 0" axis="0 0 1" frictionloss="1000"/>
                        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
                        <body name="R3" pos="0.01728 0.098 0" quat="2.01015e-11 -1 0 0">
                            <inertial pos="0.0162353 -0.0093761 0.042" quat="0.183054 0.683002 -0.183054 0.683002" mass="0.0325223" diaginertia="2.2109e-05 1.98014e-05 2.47162e-06" />
                            <joint name="R3" pos="0 0 0" axis="0 0 1" />
                            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
                            <body name="R4" pos="0.0519579 -0.0300063 0.04425">
                                <inertial pos="0.170336 0.0490038 0.00275" quat="-0.0987154 0.700182 0.0987154 0.700182" mass="0.089481" diaginertia="0.00101579 0.00101298 3.11705e-06" />
                                <joint name="R4" pos="0 0 0" axis="0 0 1" />
                                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
                            </body>
                        </body>
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

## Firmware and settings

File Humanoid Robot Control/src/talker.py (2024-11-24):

#!/usr/bin/env python
import rospy
from std_msgs.msg import String,Float32MultiArray,MultiArrayDimension
import threading
import numpy as np
import sys
sys.path.append('/home/airobots/Linkage_Robot_simulation/src')
from invk import *
import csv
import copy
import matplotlib.pyplot as plt
import pandas as pd
from Chaochi.balance import *
from Cho.function import *
from time import time as t

r_motor=[]
d_motor=[]
Step=0
index={11:0,13:1,14:2,15:3,21:4,23:5
      ,24:6,25:7,1:8,12:9,16:10,22:11,26:12}
bias=np.array([32,65,186.7,29.1,39,138.3,204.3,45.5,0,-1,0,1.5,0])# 11,13,14,15,21,23,24,25,1,12,16,22,26
limit=np.array([[51,-7],[140,55],[104.5,10],[76,-0.6],[80,22],[26,-66],[25,-70],[91,1.6]]) #要寫極限角判斷
imu_data=[0,0,0]
l_fsr=[0.0]*4
r_fsr=[0.0]*4
pos=[0.0]*13 # 對應desired
last_d=[0.0]*13

def csv2cmd(filename):
    file = open(filename)
    reader = csv.reader(file)
    data_list = list(reader)
    file.close()
    for i in range(len(data_list)):
        for j in range(len(data_list[i])):
            data_list[i][j] = float(data_list[i][j])
        data_list[i].insert(0,float(0)) #加入trunk角度
    return data_list

def dataprocess(filename):
    #讀資料
    initmotion = csv2cmd(filename)

    #左右腳馬達互換
    motionchg = copy.deepcopy(initmotion)
    for i in range(len(motionchg)):
        for j in range(1, len(motionchg[i])):
            if (j < 7):
                motionchg[i][j] = initmotion[i][j+6]
            else:
                motionchg[i][j] = initmotion[i][j-6]
            
            if (j == 2 ):
                motionchg[i][j] = motionchg[i][j]*1
            if (j == 6 ):
                motionchg[i][j] = motionchg[i][j]*1
            if (j == 8 ):
                motionchg[i][j] = motionchg[i][j]*1
            if (j ==12):
                motionchg[i][j] = motionchg[i][j]*1


    # 對動作檔進行插值(站立到準備動作)
    motion = []
    interpolation = 100
    for i in range(len(motionchg)):
        motioncol = [[0] * len(motionchg[i]) for _ in range(interpolation)]
        if i == 0:
            for j in range(len(motionchg[i])):
                temp1 = np.linspace(start = 0, stop = motionchg[i][j], num = interpolation)
                for k in range(interpolation):
                    motioncol[k][j] = temp1[k]
            for p in range(interpolation):
                motion.append(motioncol[p])
            for _ in range(50):     #準備姿勢前置多久
                motion.append(motioncol[interpolation-1])

        motion.append(motionchg[i])

    for i in range(len(motionchg)):
        motioncol = [[0] * len(motionchg[i]) for _ in range(interpolation)]
        if i == len(motionchg)-1:
            for j in range(len(motionchg[i])):
                temp1 = np.linspace(start = motionchg[i][j], stop = 0, num = interpolation)
                for k in range(interpolation):
                    motioncol[k][j] = temp1[k]
            for p in range(interpolation):
                motion.append(motioncol[p])

    return motion

def Squat_down(step,desired):
    right=np.array([-0.0115,-0.00725,-1.0307])
    left=np.array([-0.0115,-0.00725,-1.0307])
    if step > 100:
        time=step-100
        desired[1:7]=InvK(left+com_sin_trace(time,[0,0,0.05],500))
        desired[7:]=InvK(right+com_sin_trace(time,[0,0,0.05],500))
    return desired

def Swing(step,desired):
    right=np.array([-0.0115,-0.00725,-1.0307])
    left=np.array([-0.0115,-0.00725,-1.0307])
    if step > 200:
        time=step-200
        desired[1:7]=InvK(left+com_sin_trace(time,[0,0.1,0],500))
        desired[7:]=InvK(right+com_sin_trace(time,[0,0.1,0],500))
    return desired


def get_cmd(motor,desired):
    reset = 0
    global Step, pos, r_motor,d_motor
    init_pos_r=[0,0,0] #20 40
    init_pos_l=[0,0,0] #20 40
    if reset:
        desired=[0.0]*13
        init_pos_l=[22,40,20] #20 40
        init_pos_r=[22,42,21] #20 40 
    motor[index[11]][:3]=np.array([11,4,bias[0]],dtype=np.float64)
    motor[index[13]][:3]=np.array([13,4,-desired[9]+bias[1]+init_pos_r[0]],dtype=np.float64)
    motor[index[14]][:3]=np.array([14,4,desired[10]+bias[2]+init_pos_r[1]],dtype=np.float64)
    motor[index[15]][:3]=np.array([15,4,-desired[11]+bias[3]+init_pos_r[2]],dtype=np.float64)
    motor[index[21]][:3]=np.array([21,4,bias[4]],dtype=np.float64)
    motor[index[23]][:3]=np.array([23,4,desired[3]+bias[5]-init_pos_l[0]],dtype=np.float64)
    motor[index[24]][:3]=np.array([24,4,-desired[4]+bias[6]-init_pos_l[1]],dtype=np.float64)
    motor[index[25]][:3]=np.array([25,4,desired[5]+bias[7]-init_pos_l[2]],dtype=np.float64)
    motor[index[1]][:2]=np.array([1,desired[0]+bias[8]],dtype=np.float64)
    motor[index[12]][:2]=np.array([12,desired[8]+bias[9]],dtype=np.float64)
    motor[index[16]][:2]=np.array([16,desired[12]+bias[10]],dtype=np.float64)
    motor[index[22]][:2]=np.array([22,desired[2]+bias[11]],dtype=np.float64)
    motor[index[26]][:2]=np.array([26,desired[6]+bias[12]],dtype=np.float64)
    
    
    # for i in range(8):
    #     if limit[i][0]<motor[i][2]:
    #         motor[i][2]=limit[i][0]
    #     elif limit[i][1]>motor[i][2]:
    #         motor[i][2]=limit[i][1]
    
    if Step<300:
            r_motor.append(pos)
    if Step==299:
        print("plot")
        r_motor = np.array(r_motor)
        pd.DataFrame(r_motor).to_csv("localcom/Cho/return.csv",header=None,index=False)
    Step+=1
    
    return motor

def command():
    global imu_data
    global pos
    # MyActuator mode
    # 'shut_down': 0,  # torque off
    # 'stop': 1,   # still torque on
    # 'torque': 2,
    # 'speed': 3,
    # 'position': 4,
    # 'pos_increment': 5,
    # 'angle': 6,
    # 'status': 7,
    # 'reset': 8, # switch between motion and normal mode
    # 'torque_off': 9,
    # 'torque_on': 10
    # 'motion_cmd': 11
    pub = rospy.Publisher('command', Float32MultiArray, queue_size=10)
    rate = rospy.Rate(50) # Hz
    step=0
    desired=np.array([0.0]*13)
    # motion = dataprocess('src/F2_train3.csv')  # YenMing Chen
    motion = csv2cmd('localcom/Cho/F2.csv' )  # Mr. Draw

    while not rospy.is_shutdown():
        # add control code & data proccess & algorithm
        # cmd [id,mode,target value] MyActuator
        # if mode == 11 cmd [id,mode,pos, vel, t_ff, kp=10.012, kd=1]
        # cmd [id,target value] dynamixal
        motor=-np.ones((13,7)) #[11,13,14,15,21,23,24,25,1,12,16,22,26]
        # desired=Squat_down(step,desired)
        desired=Walk(step, desired, motion)
        # desired=balance_angle(desired,imu_data,pos,l_fsr,r_fsr,0)
        
        motor = get_cmd(motor,desired)
        cmd = Float32MultiArray(None,list(motor.reshape(13*7)))
        
        pub.publish(cmd)
        rate.sleep()
        step+=1

def recieve():
    rate = rospy.Rate(50)
    rospy.Subscriber('sensor', Float32MultiArray, callback)
    while not rospy.is_shutdown():
        rate.sleep()

def callback(data):
    global imu_data
    global pos
    global l_fsr
    global r_fsr
    # recieve sensor data & motor status
    status=np.array(data.data).reshape(16,4)
    imu_data = status[-3][:3]
    l_fsr = status[-2]
    r_fsr = status[-1]
    pos = [status[index[1]][1]-bias[index[1]],status[index[21]][1]-bias[index[21]],status[index[22]][1]-bias[index[22]],
           status[index[23]][1]-bias[index[23]],-(status[index[24]][1]-bias[index[24]]),status[index[25]][1]-bias[index[25]],
           status[index[26]][1]-bias[index[26]],status[index[11]][1]-bias[index[11]],status[index[12]][1]-bias[index[12]],
           -(status[index[13]][1]-bias[index[13]]),status[index[14]][1]-bias[index[14]],-(status[index[15]][1]-bias[index[15]]),
           status[index[16]][1]-bias[index[16]]]
    # print(pos)
    # print(r_fsr)
    # print("Motor status")
    # print("ID: {}, Current: {} A, Speed: {} dps, Degree: {},Torque: {}".format(status[0],status[1],status[2],status[3],status[4],status[5]))
    # rospy.loginfo(rospy.get_caller_id() + 'I heard %s', data.data)

if __name__ == '__main__':
    try:
        rospy.init_node('commander', anonymous=True)
        sub = threading.Thread(target = recieve)
        pub = threading.Thread(target = command)
        sub.start()
        pub.start()
        sub.join()
        pub.join()
    except rospy.ROSInterruptException:
        pass

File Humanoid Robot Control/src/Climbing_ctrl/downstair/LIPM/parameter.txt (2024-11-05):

one-step on stair:
Com1 = 0.03, Com2 = 0.09
""" Setting of LIPM parameters """
        # Amplitude of swing
        b1 = -0.215
        b2 = 0.211

        # Motor 31/35 and Motor 41/45
        # 正： 腰與腳踝彎曲方向一致 #調小重心轉換沒那麼過去!
        hip1 = 0.26
        hip2 = 0.24

        # Step Height
        stepHeight1 = 0.1
        stepHeight2 = 0.15

        # Forward Distance
        stepSize1 = 0.25
        stepSize2 = 0.27

        # Lateral Displacement
        shift1 = [0.0, 0]
        shift2 = [0, 0.0]

        # Motor 30 and Motor 40
        yawAngleR = [[0, 0, 0, 0, 0], [0, 0, 0, 0, 0]]  # 正: 往外開
        yawAngleL = [[0, 0, 0, 0, 0], [0, 0, 0, 0, 0]]  # 正: 往外開

        # Motor 34 and Motor 44
        initLeanAngleR = 0
        initLeanAngleL = 0
        leanAngleR = [[0, 0, 0, 0, 0], [0, -5, -4, -3, -3]]  # 正: 腳尖向up
        leanAngleL = [[0, 0, 0, 0, 0], [0, 3, -8, -10, -10]]  # 正: 腳尖向下

        # Motor 35 and Motor 45 
        pedalRollAngleR = [[0, 0, 0, 0, 0], [0, 0, 0, 0, 0]]    # 正: 往內番
        pedalRollAngleL = [[0, 0, 0, 0, 0], [0, 0, 0, 0, 0]]   # 正: 往內番


two-step on stair * 2:
Com = 0.05 & 0.06 only QQ
""" Setting of LIPM parameters """
        # Amplitude of swing
        b1 = -0.215
        b2 = 0.211

        # Motor 31/35 and Motor 41/45
        # 正： 腰與腳踝彎曲方向一致 #調小重心轉換沒那麼過去!
        hip1 = 0.26
        hip2 = 0.24

        # Step Height
        stepHeight1 = 0.1
        stepHeight2 = 0.1

        # Forward Distance
        stepSize1 = 0.26
        stepSize2 = 0.

        # Lateral Displacement
        shift1 = [0.0, 0]
        shift2 = [0, 0.0]

        # Motor 30 and Motor 40
        yawAngleR = [[0, 0, 0, 0, 0], [0, 0, 0, 0, 0]]  # 正: 往外開
        yawAngleL = [[0, 0, 0, 0, 0], [0, 0, 0, 0, 0]]  # 正: 往外開

        # Motor 34 and Motor 44
        initLeanAngleR = 0
        initLeanAngleL = 0
        leanAngleR = [[0, 0, 0, 0, 0], [0, -5, -4, -5, -3]]  # 正: 腳尖向up
        leanAngleL = [[0, 0, 0, 0, 0], [0, 3, 3, 0, 0]]  # 正: 腳尖向下

        # Motor 35 and Motor 45 
        pedalRollAngleR = [[0, 0, 0, 0, 0], [0, 0, 0, 0, 0]]    # 正: 往內番
        pedalRollAngleL = [[0, 0, 0, 0, 0], [0, 0, 0, 0, 0]]   # 正: 往內番


two-step on stair * 2:
Com = 0.08
""" Setting of LIPM parameters """
        # Amplitude of swing
        b1 = -0.215
        b2 = 0.211

        # Motor 31/35 and Motor 41/45
        # 正： 腰與腳踝彎曲方向一致 #調小重心轉換沒那麼過去!
        hip1 = 0.26
        hip2 = 0.24

        # Step Height
        stepHeight1 = 0.1
        stepHeight2 = 0.1

        # Forward Distance
        stepSize1 = 0.26
        stepSize2 = -0.03

        # Lateral Displacement
        shift1 = [0.0, 0]
        shift2 = [0, 0.0]

        # Motor 30 and Motor 40
        yawAngleR = [[0, 0, 0, 0, 0], [0, 0, 0, 0, 0]]  # 正: 往外開
        yawAngleL = [[0, 0, 0, 0, 0], [0, 0, 0, 0, 0]]  # 正: 往外開

        # Motor 34 and Motor 44
        initLeanAngleR = 0
        initLeanAngleL = 0
        leanAngleR = [[0, 0, 0, 0, 0], [0, -5, -8, -5, -3]]  # 正: 腳尖向up
        leanAngleL = [[0, 0, 0, 0, 0], [0, 5, 5, 0, 0]]  # 正: 腳尖向下

        # Motor 35 and Motor 45 
        pedalRollAngleR = [[0, 0, 0, 0, 0], [0, 0, 0, 0, 0]]    # 正: 往內番
        pedalRollAngleL = [[0, 0, 0, 0, 0], [0, 0, 0, 0, 0]]   # 正: 往內番


two-step on stair * 2:
Com = 0.08, 0.09, 0.1, 0.11
""" Setting of LIPM parameters """
        # Amplitude of swing
        b1 = -0.215
        b2 = 0.211

        # Motor 31/35 and Motor 41/45
        # 正： 腰與腳踝彎曲方向一致 #調小重心轉換沒那麼過去!
        hip1 = 0.26
        hip2 = 0.24

        # Step Height
        stepHeight1 = 0.13
        stepHeight2 = 0.13

        # Forward Distance
        stepSize1 = 0.26
        stepSize2 = -0.0

        # Lateral Displacement
        shift1 = [0.0, 0]
        shift2 = [0, 0.0]

        # Motor 30 and Motor 40
        yawAngleR = [[0, 0, 0, 0, 0], [0, 0, 0, 0, 0]]  # 正: 往外開
        yawAngleL = [[0, 0, 0, 0, 0], [0, 0, 0, 0, 0]]  # 正: 往外開

        # Motor 34 and Motor 44
        initLeanAngleR = 0
        initLeanAngleL = 0
        leanAngleR = [[0, 0, 0, 0, 0], [0, -5, -6, -5, -3]]  # 正: 腳尖向up
        leanAngleL = [[0, 0, 0, 0, 0], [0, 5, 5, 0, 0]]  # 正: 腳尖向下

        # Motor 35 and Motor 45 
        pedalRollAngleR = [[0, 0, 0, 0, 0], [0, 0,  0,  0, 0]]    # 正: 往內番
        pedalRollAngleL = [[0, 0, 0, 0, 0], [0, 0, -4, -4, 0]]   # 正: 往內番
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

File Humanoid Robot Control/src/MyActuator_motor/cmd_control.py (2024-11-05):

import can
import time

'''
This function aims to assign command for motor.
Args:
    control : string  control type
    val : int control value
return list, that will be transmitted
'''
def get_data(control, val):
    data = [0]*8

    # Convert control option to hex.
    # Shut down will cause motor torque off, while stop will be torque on.
    c_option = {
        'shut_down': 0x80,  # torque off
        'stop': 0x81,   # still torque on
        'torque': 0xA1,
        'speed': 0xA2,
        'position': 0xA4,
        'pos_increment': 0xA8,
        'angle': 0x92,
        'status': 0x9C,
        'torque_off': 0x77,
        'torque_on': 0x78
    }
    data[0] = c_option[control]  # data[0] is based on cmd type

    # Last part is 00 cmd, most of them are getting information from motor.
    if control == 'shut_down' or control == 'stop':
        data[1] = data[2] = data[3] = data[4] = data[5] = data[6] = data[7] = 0x00

    elif control == 'torque' or control == 'speed':
        data[1] = data[2] = data[3] = 0x00
        hex_val = val_trans_8(val)  # Value transform
        for i in range(4):
            data[4+i] = hex_val[i]

    elif control == 'position':
        data[1] = 0x00
        # data[2],[3] represent motor speed in dps(degree per second). [3] is high, [2] is low. Here 0x01F4 is 500dps
        data[2] = 0xF4
        data[3] = 0x01
        hex_val = val_trans_8(val)  # Value transform
        for i in range(4):
            data[4+i] = hex_val[i]

    elif control == 'pos_increment':
        data[1] = 0x00
        # data[2],[3] represent motor speed in dps(degree per second). [3] is high, [2] is low. 0x01F4 is 500 dps
        data[2] = 0xF4
        data[3] = 0x01
        hex_val = val_trans_8(val)  # Value transform
        for i in range(4):
            data[4+i] = hex_val[i]

    return data


'''
Fuction for decimal to hex
Args:
    param dec
return list, hexdicemal list
'''
def val_trans_8(dec):
    # According to 0.01 degree/LSB, input value must be 100 times larger.
    dec = dec * 100

    # Negative need to be modified before transformed to hex
    if dec < 0:
        dec = dec+2**32

    # low to high
    hex_data = []
    dec = int(dec)
    str = '{:08X}'.format(dec)
    for i in range(4):
        hex_data.append(int(str[6-i*2:8-i*2], 16))

    return hex_data


'''
Send msg to CAN bus
Args:
    param id
    param control
    param val
'''
def send_msg(bus, id, control, val):
    data = get_data(control, val)

    # Basic message formats
    msg = can.Message(
        arbitration_id=id, data=data, extended_id=False
    )

    try:
        bus.send(msg)
        # print(f"Message sent on {bus.channel_info}")
    except can.CanError:
        print("Message NOT sent")


if __name__ == "__main__":
    # Setting CAN bus
    bus = can.Bus(interface='socketcan', channel='can0', bitrate=1000000)
    # send_msg(bus, 0x141, 'stop', 200)
    # send_msg(bus, 0x142, 'stop', 200)
    send_msg(bus, 0x141, 'position', 0)
    # send_msg(bus, 0x142, 'position', 0)

    # for i in range(10):
    #     send_msg(bus, 0x141, 'speed', 200)
    #     send_msg(bus, 0x142, 'speed', 200)
    #     time.sleep(5)
    #     print("spd over!")

    #     send_msg(bus, 0x141, 'position', 200)
    #     send_msg(bus, 0x142, 'position', 200)
    #     time.sleep(2)
    #     print("pos over!")

    #     send_msg(bus, 0x141, 'status', 200)
    #     send_msg(bus, 0x142, 'status', 200)
    #     time.sleep(3)
    #     print("wait!")

    #     send_msg(bus, 0x141, 'speed', 200)
    #     send_msg(bus, 0x142, 'speed', 200)
    #     send_msg(bus, 0x141, 'angle', 200)
    #     send_msg(bus, 0x142, 'angle', 200)
    #     time.sleep(2)
    #     print("angle!")

    #     send_msg(bus, 0x141, 'stop', 200)
    #     send_msg(bus, 0x142, 'stop', 200)
    #     time.sleep(1)
    #     print("stop!")

    #     send_msg(bus, 0x141, 'pos_increment', 200)
    #     send_msg(bus, 0x142, 'pos_increment', 200)
    #     print("INC!")
    #     time.sleep(10)

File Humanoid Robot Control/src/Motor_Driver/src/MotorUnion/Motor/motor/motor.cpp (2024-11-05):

#include "motor.h"
#include <iostream>
using namespace std;
motor::motor()
{
	Angle2MotorScale = 0.0f;
	MotorScale2Angle = 0.0f;
	Scale2RPM = 0.0f;
	Scale2RPMM = 0.0f;

	Motor_Operating_Mode = 3;
	Motor_CenterScale = 0;
	Motor_Angle = 0.0f;
	Motor_Scale = 0;
	Motor_Velocity = 0.0f;
	Motor_Current = 0.0f;
	Motor_Accel = 0.0f;
	Motor_Present_Angle = 0.0f;
	Motor_Present_Velocity = 0.0f;
	Motor_Present_Current = 0.0f;
	Motor_TorqueEnable = false;

	Max_Position_Limit = 0;
	Min_Position_Limit = 0;
	Max_Velocity_Limit = 0;
	Min_Velocity_Limit = 0;
	Max_Extend_Limit = 0;
	Min_Extend_Limit = 0;
	Max_Accel_Limit = 0;
	Max_Current_Limit = 0;
	Min_Current_Limit = 0;

	is_Arrival = true;
	is_Write_Scale = false;
	is_Write_Velocity = false;
	is_Write_Accel = false;
	is_Write_Current = false;
	is_Write_TorqueEnable = false;
}
//-----------------------------------------------------//
const int &motor::GetMotor_Operating_Mode() const { return Motor_Operating_Mode; }

const float &motor::GetMotor_Scale2RPM() const { return Scale2RPM; }

const float &motor::GetMotor_Scale2RPMM() const { return Scale2RPMM; }

const short &motor::GetMotor_CenterScale() const { return Motor_CenterScale; }

const float &motor::GetMotor_Angle() const { return Motor_Angle; }

const float &motor::GetMotor_Velocity() const { return Motor_Velocity; }

const float &motor::GetMotor_Accel() const { return Motor_Accel; }

const float &motor::GetMotor_Current() const { return Motor_Current; }

const bool &motor::GetMotor_TorqueEnable() const { return Motor_TorqueEnable; }

const float &motor::GetMotor_PresentAngle() const { return Motor_Present_Angle; }

const float &motor::GetMotor_PresentVelocity() const { return Motor_Present_Velocity; }

const float &motor::GetMotor_PresentCurrent() const { return Motor_Present_Current; }

const bool &motor::GetMotor_Arrival() const { return is_Arrival; }
//-----------------------------------------------------//
void motor::SetMotor_Operating_Mode(const int &operating_mode)
{
	Motor_Operating_Mode = operating_mode;
}

void motor::SetMotor_CenterScale(const short &centerscale)
{
	Motor_CenterScale = centerscale;
}
void motor::SetMotor_Angle(const float &angle)
{
	switch (Motor_Operating_Mode)
	{
	case 1: // Velocity control mode
	case 3: // Position control mode
		Motor_Scale = round(angle * Angle2MotorScale + Motor_CenterScale);
		if (Motor_Scale >= Max_Position_Limit)
			Motor_Scale = Max_Position_Limit;
		else if (Motor_Scale <= Min_Position_Limit)
			Motor_Scale = Min_Position_Limit;
		else
			;
		Motor_Angle = (Motor_Scale - Motor_CenterScale) * MotorScale2Angle;
		break;
	case 4: // Extended position control mode
		Motor_Scale = round(angle / 360 * Rev_Resol_Extended);
		if (Motor_Scale >= Max_Extend_Limit)
			Motor_Scale = Max_Extend_Limit;
		else if (Motor_Scale <= Min_Extend_Limit)
			Motor_Scale = Min_Extend_Limit;
		else
			;
		Motor_Angle = (float)Motor_Scale / Rev_Resol_Extended * 360;

		break;
	}

	is_Arrival = false;
	is_Write_Scale = true;
}

void motor::SetMotor_Velocity(const float &velocity)
{
	switch (Motor_Operating_Mode)
	{
	case 1: // Velocity control mode
		if (velocity >= Max_Velocity_Limit)
			Motor_Velocity = Max_Velocity_Limit;
		else if (velocity <= Min_Velocity_Limit)
			Motor_Velocity = Min_Velocity_Limit;
		else
			Motor_Velocity = velocity;
		break;

	case 3: // Position control mode
	case 4: // Extended position control mode
		if (std::abs(velocity) >= Max_Velocity_Limit)
			Motor_Velocity = Max_Velocity_Limit;
		else
			Motor_Velocity = std::abs(velocity);
		break;
	}
	is_Write_Velocity = true;
}

void motor::SetMotor_Accel(const float &accel)
{
	if (accel >= Max_Accel_Limit)
		Motor_Accel = Max_Accel_Limit;
	else
		Motor_Accel = accel;

	is_Write_Accel = true;
}
void motor::SetMotor_Current(const float &current)
{
	// cout << Motor_Operating_Mode << endl;
	switch (Motor_Operating_Mode)
	{
	case 0: // Current control mode
		if (current >= Max_Current_Limit)
			Motor_Current = Max_Current_Limit;
		else if (current <= Min_Current_Limit)
			Motor_Current = Min_Current_Limit;
		else
			Motor_Current = current;
		break;
	case 1: // Velocity control mode
	case 3: // Position control mode
	case 4: // Extended position control mode
		;
	}
	is_Write_Current = true;
}
void motor::SetMotor_TorqueEnable(const bool &enable)
{
	Motor_TorqueEnable = enable;
	is_Write_TorqueEnable = true;
}

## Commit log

2024-11-05 Human-Robot Collaboration of Intelligent Bipedal Robots in MultiLevel Warehousing
    [0125_forward_cmd_ALL.csv, B_data.csv, B_data_ori.csv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]
2024-11-18 add Humanoid Robot Mechanism
    [30_40_Hip motor board(back).sldprt, 30_40_Hip motor board(front).sldprt, 30_40_Hip.SLDASM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]
2024-11-18 add MotorUnion architecture
2024-11-22 remove Humanoid Robot Control
    [0125_forward_cmd_ALL.csv, B_data.csv, B_data_ori.csv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]
2024-11-22 new_folder from Lab
    [0125_forward_cmd_ALL.csv, B_data.csv, B_data_ori.csv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]
2024-11-24 revise error in report
    [talker.py]
